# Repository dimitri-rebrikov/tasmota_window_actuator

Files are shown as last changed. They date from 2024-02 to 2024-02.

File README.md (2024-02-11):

# Tasmota based window actuator
This project implements a [tasmota](https://tasmota.github.io) based windows actuator.

The implementation allows steer the window both directly using buttons and remotely over the functionalities provided by tasmota (MQTT, HTTT, Web UI).

I integrated the actuator into my [OpenHab](https://www.openhab.org/) environment, which is also described below.

## Circuit Diagram

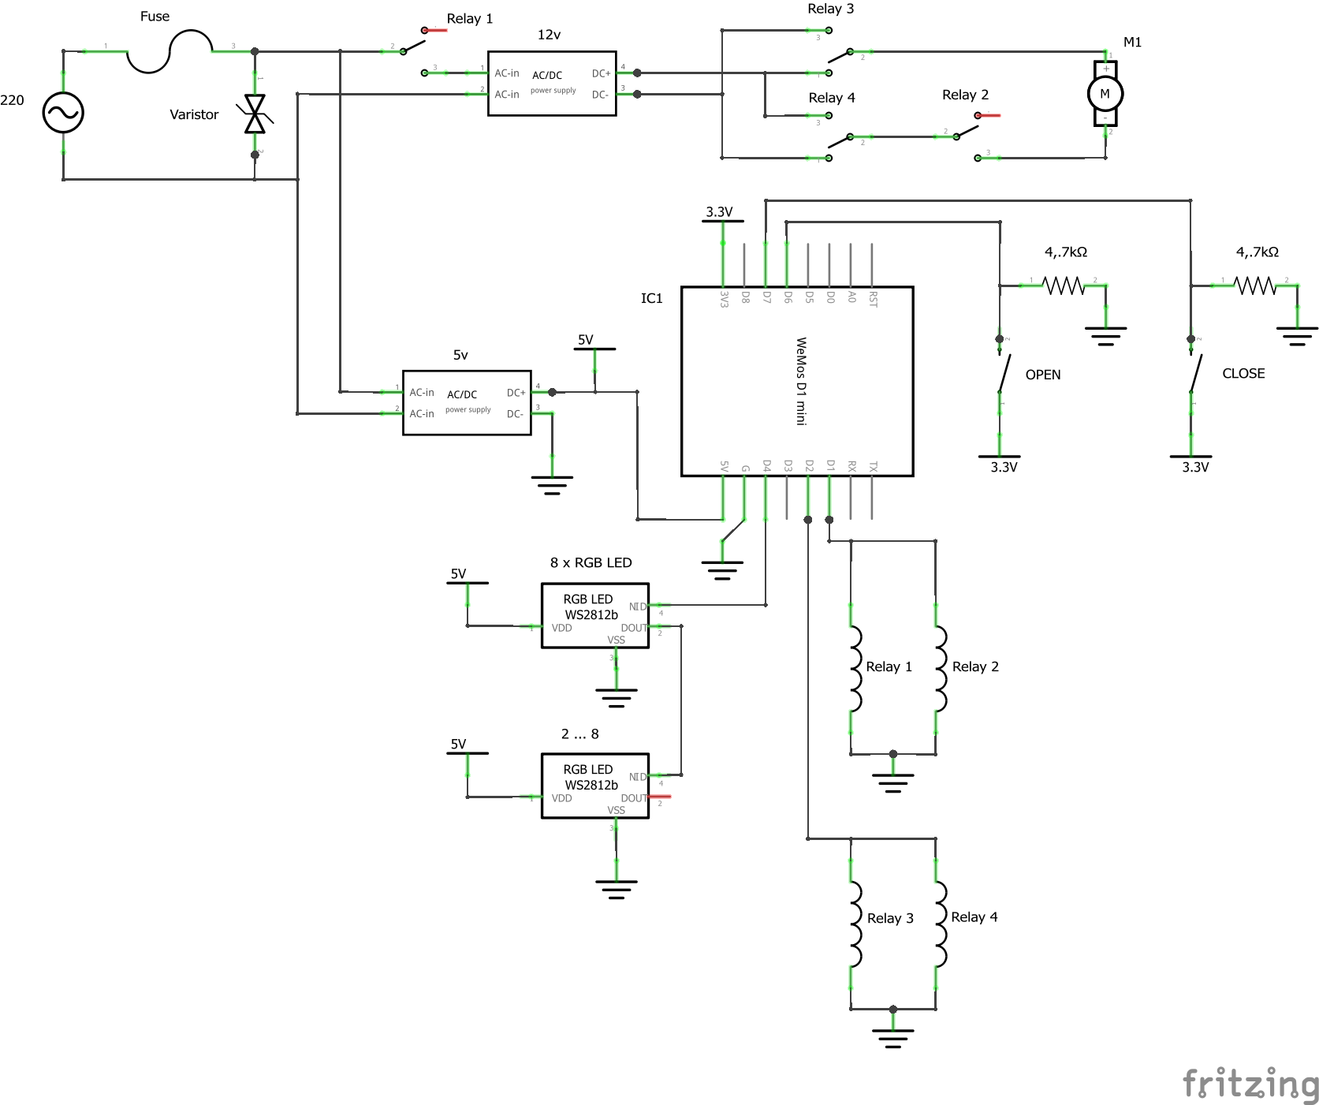
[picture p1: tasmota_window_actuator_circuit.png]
Circuit Diagramm


### Relay 1
Powers the 12v power supply only if needed

### Relay 2
Switch on/off the motor. The Relay 1 is not enough as the remaining energy of the power supply continues to power the motor even if the power supply by itself is cut off the current. So Relay 2 ensures immediate stop of the motor.

### Relays 3 and 4 
Are the classic power polarity inverting circuit. Together they let the motor turn into the one or another direction.

### Push Buttons "OPEN" and "CLOSE"
The buttons are implemented with the pull-up resistors.

### 8 x RGB LED WS2512b (optional)
This is an optional/changeable component to visualize the current status of the window.
In the presented implementation it is a stripe of 8 RGB LEDs.

### Fuse and Varistor
Shall protect the circuit.

### Motor
I used a linear actuator for 12v

### WeMos D1 mini
Is the "Brain" of the circuit.

## Assembly

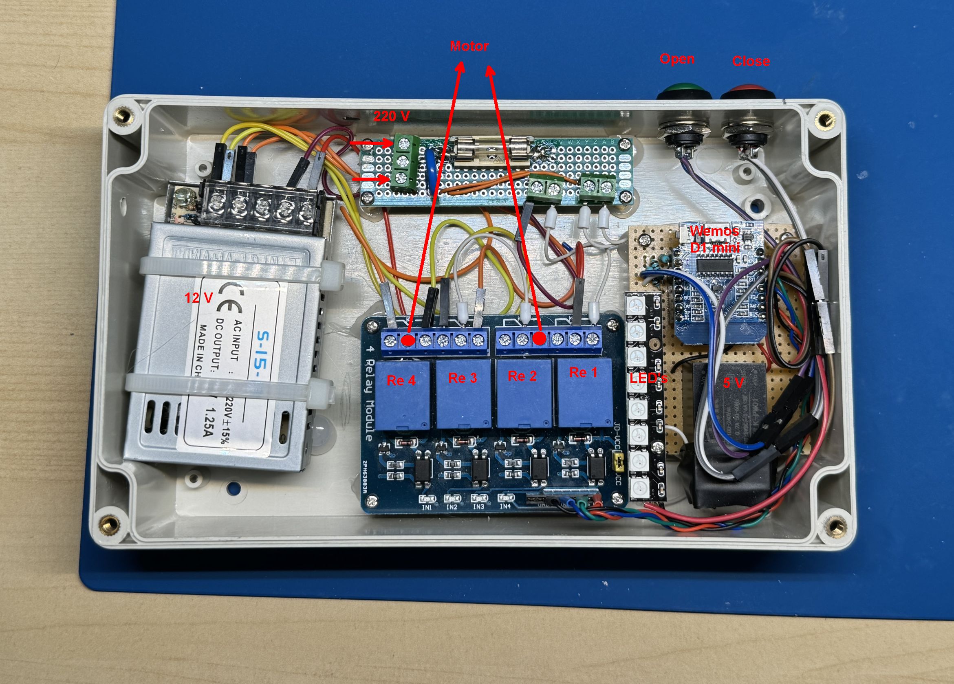
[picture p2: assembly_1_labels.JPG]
Assembly


## Tasmota Configuration

### Module Configuration

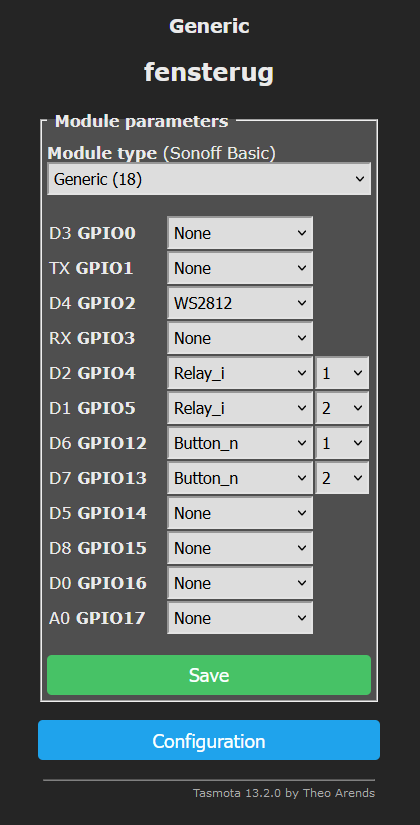
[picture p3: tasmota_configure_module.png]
Module Configuration


### Settings and Rules

#### Motor and Buttons
Configure motor and button functionality using the tasmota build-in shutter&blinds support:
```
Backlog SetOption80 1; ShutterRelay1 1; ShutterMode 2; Interlock OFF; ShutterButton1 2 up 0; ShutterButton1 1 down 0; ShutterCloseDuration1 23; ShutterOpenDuration1 23
```

#### LED's (Optional)
Configure LED's to show the open/close status but also the opening/closing progress:
```
Rule1
	on system#boot do backlog led1 000000; led2 000000; led3 000000; led4 000000; led5 000000; led6 000000; led7 000000; led8 000000 endon
	ON Shutter1#Position=0 DO backlog led1 100000; led2 000000; led3 000000; led4 000000; led5 000000; led6 000000; led7 000000; led8 000000 endon
	ON Shutter1#Position=100 DO backlog delay 1; led1 000000; led2 000000; led3 000000; led4 000000; led5 000000; led6 000000; led7 000000; led8 001000 endon
	ON Shutter1#Position>=15 DO led2 050500 endon
	ON Shutter1#Position<15 DO led2 000000 endon
	ON Shutter1#Position>=30 DO led3 050500 endon
	ON Shutter1#Position<30 DO led3 000000 endon
	ON Shutter1#Position>=45 DO led4 050500 endon
	ON Shutter1#Position<45 DO led4 000000 endon	
	ON Shutter1#Position>=60 DO led5 050500 endon
	ON Shutter1#Position<60 DO led5 000000 endon
	ON Shutter1#Position>=75 DO led6 050500 endon
	ON Shutter1#Position<75 DO led6 000000 endon
	ON Shutter1#Position>=90 DO led7 050500 endon
	ON Shutter1#Position<90 DO led7 000000 endon

Rule1 1
```

## Integration Into OpenHab

### OpenHab
First of all you need a local [OpenHab](https://www.openhab.org/) server.

### MQTT Broker
The second prerequisite is a MQTT Broker. I installed the [Mosquitto](https://mosquitto.org/)

### Integrate MQTT Broker into OpenHab
1. Add the MQTT Binding Add-on to you OpenHab
2. Configure the MQTT Broker connection

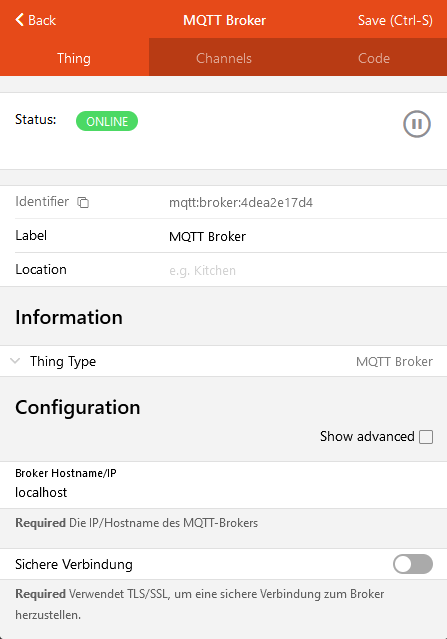
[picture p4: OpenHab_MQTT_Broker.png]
OpenHab MQQT Broker Connection


### Configure Tasmota to interact with the MQTT Broker
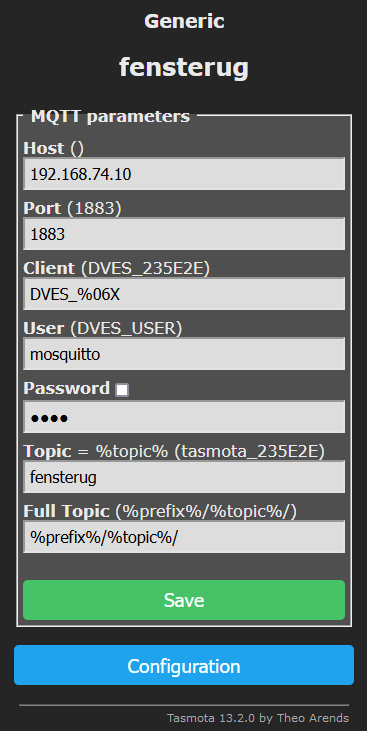
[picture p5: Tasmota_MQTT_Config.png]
Tasmota MQTT Configuration


### Integrate the Window Actor over the MQTT Broker into OpenHab
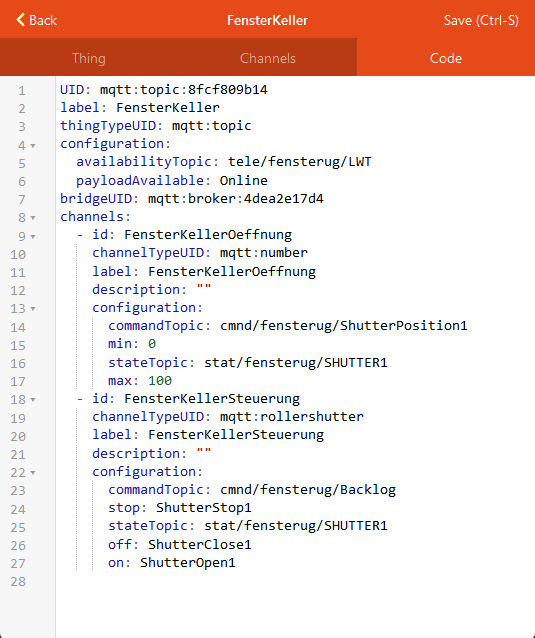
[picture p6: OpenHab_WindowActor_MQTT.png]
OpenHab Window Actor integarion


Here 2 channels are integrated:
- Information Channel providing the info about opening status of the window actor
- Command Channel allowing sending open/close commands

For the command channel a workaround over the Backlog command is used allowing sending the tasmota console commands over this channel.

### Use the Windows Actor in the OpenHab rules
After the connection between OpenHab and the Windows Actor is configured it can be used in the OpenHab rules to react to events like pressing virtual buttons or to some other events like, in my case, to switching on/off of the haze extractor hood:

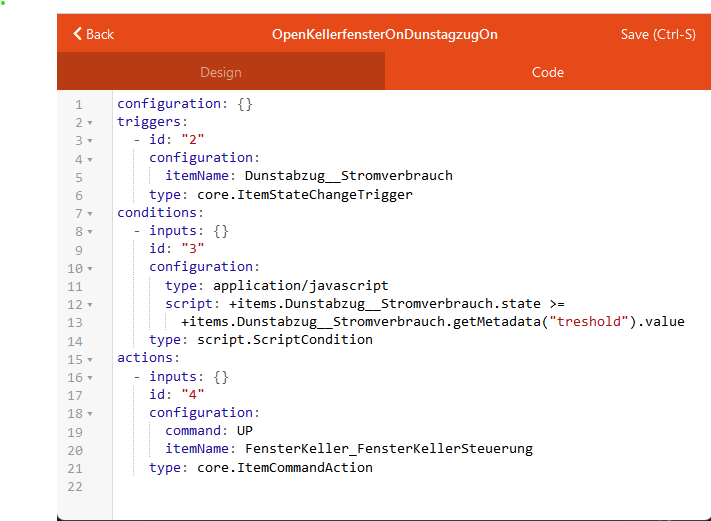
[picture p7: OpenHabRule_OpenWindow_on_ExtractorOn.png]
OpenHab Rule to open the Window on switching on of the Extractor Hood


Here if the power consumption of the extractor hood exceeds the specified threshold value the command "UP" is send to the `cmnd/fensterug/Backlog` topic of the Windows Actor resulting the opening of the window.

The opposite rule looks like following:

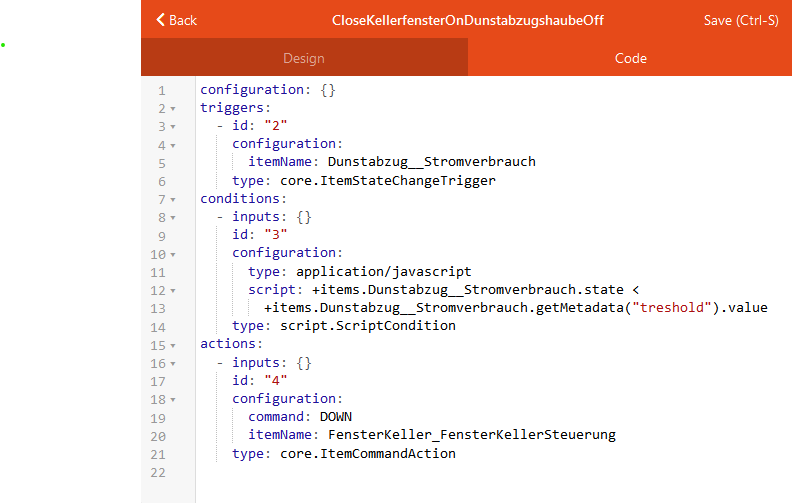
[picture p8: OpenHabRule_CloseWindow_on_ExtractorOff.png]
OpenHab Rule to close the Window on switching off of the Extractor Hood


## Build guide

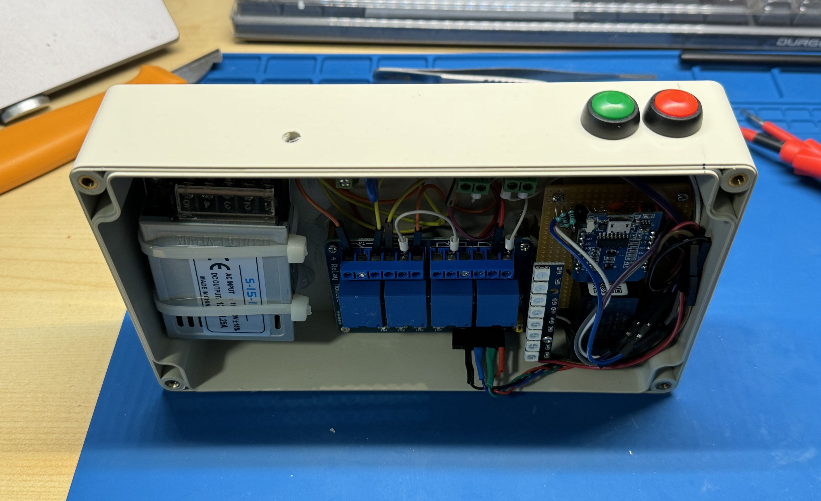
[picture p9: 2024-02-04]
assembly_4.JPG

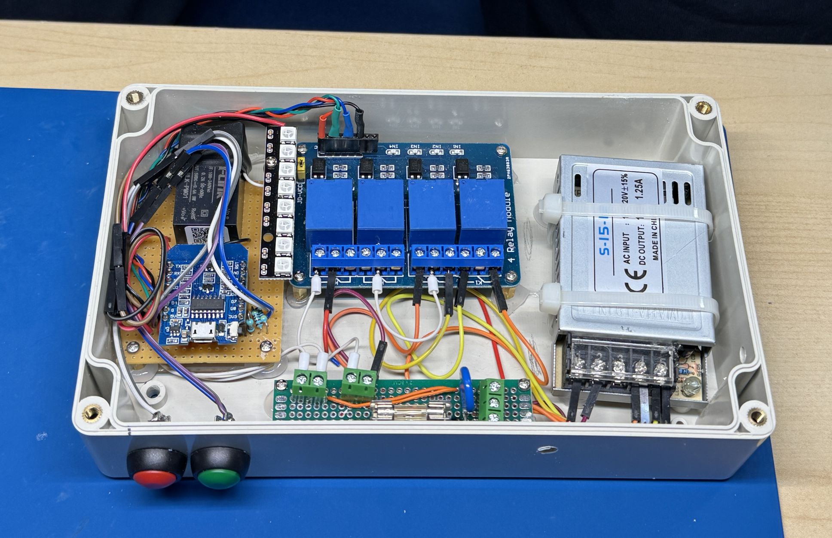
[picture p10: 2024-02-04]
assembly_2.JPG

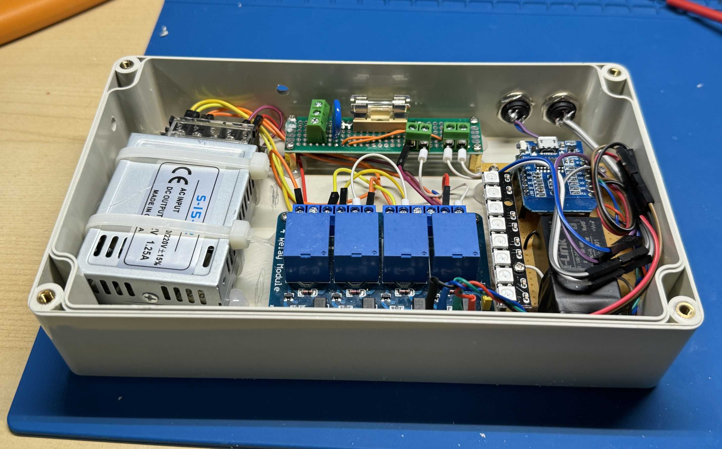
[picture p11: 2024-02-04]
assembly_3.JPG
